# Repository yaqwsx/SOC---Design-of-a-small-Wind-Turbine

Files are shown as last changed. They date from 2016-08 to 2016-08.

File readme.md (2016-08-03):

Český popis k nalezení níže.

# Design of a Small Wind Turbine

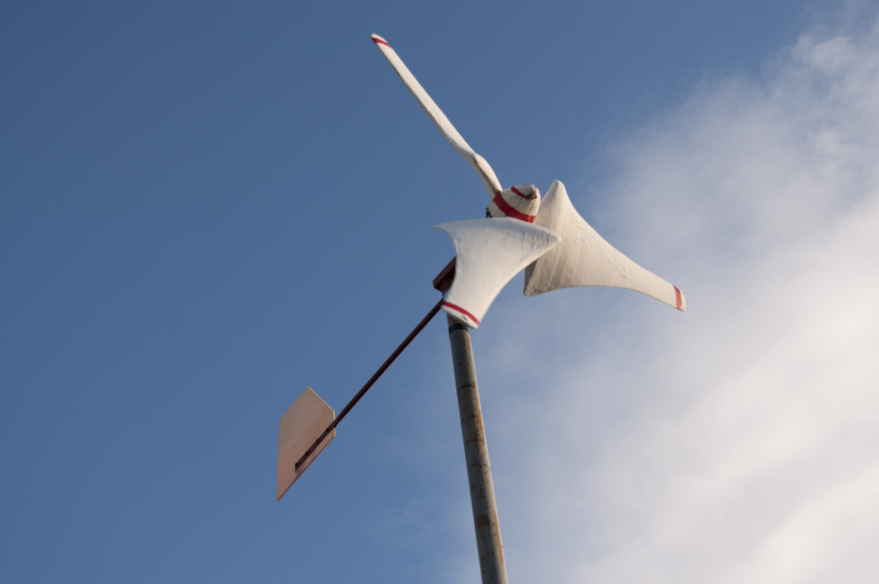
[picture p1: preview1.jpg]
preview1


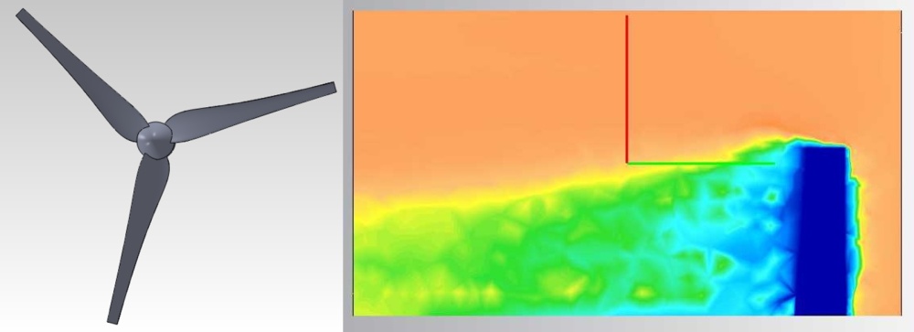
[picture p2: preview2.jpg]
preview2


This is a backup of my high school project created back in 2012. It is a direct
copy, without any modification. Because I was stupid when I was a kid, the
source is quite messy.

I explore aerodynamics principles of wind turbines in this thesis and based on
these principles I design a small turbine width diameter 2.5 meters. I discuss
aspects of its efficiency, startability and ways to reduce induced loss. The
induced losses were explored by a FEM simulation.

The whole thesis in Czech, but even though you might want to check out the [final
version](text_v2/final.pdf) - there are lots of images and a nice formulas! The
thesis won a 2nd place in [SOČ](http://soc.cz).

Small note: Three years later I build a turbine according design in this theses.
However there are no photos, as my SD card with them died. Since then, I backup!
(and you should too). See more at [Aurae repostiory](https://github.com/yaqwsx/Aurae).

# Návrh malé větrné turbíny

Tento repozitář je záložní kopií mého středoškolského projektu z roku 2012.
Projekt nebyl nijak modifikován a je v původní (lehce chaotické) verzi.

Práce se zabývá aerodynamikou malých větrných turbín a zejména jejich návrhem.
Popisuje návrh malé horizontální větrné turbíny o průměru 2,5 m. Zkoumá různé
aspekty její účinnosti, zabývá se její startovatelností a omezením indukovaných
ztrát. Práce dále popisuje také stavbu druhé menší turbíny založené na
zjednodušeném výpočtu.

Práce vyhrála 2. místo na [SOČ](http://soc.cz). Finální verze textu je k
nalezení [zde](text_v2/final.pdf).

Poznámka na závěr: Tři roky po napsání této práce jsem skutečně postavil turbínu
popisovou v této práci. Bohužel k ní nemám žádnou dokumentaci, jelikož SD karta
s veškerými fotografiemi umřela. Od té doby zálohuji! Více informací je k nalezení
v [repozitáři Aurae](https://github.com/yaqwsx/Aurae).

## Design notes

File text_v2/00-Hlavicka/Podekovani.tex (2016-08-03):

\vfill

\vglue 14cm

\section*{Poděkování}

\begin{spacing}{1.3}
Chtěl bych poděkovat zejména mému otci, který mě v~celém mém bádání podporuje a poskytuje mi pomoc v~konstrukčních stránkách celé stavby. 
\end{spacing}

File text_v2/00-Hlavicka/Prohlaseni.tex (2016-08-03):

\vfill

\vglue 13cm

\section*{Prohlášení}

\begin{spacing}{1.3}
	 Prohlašuji, že jsem svou práci vypracoval samostatně, použil jsem pouze podklady (literaturu, software, atd.) uvedené v této práci a postup při zpracování a dalším nakládání s prací je v souladu se zákonem č. 121/2000 Sb., o právu autorském, o právech souvisejících s právem autorským a o změně některých zákonů (autorský zákon) v~platném znění. 
\end{spacing}

\vspace{1.5cm}

V~Hulíně dne \Podepsano

\begin{flushright}
	\vspace{-1.5cm}
	\begin{tabular}{p{3.5cm}}
		\hspace{0.8cm}
		\\
		\hline
		\hspace{1cm} podpis
	\end{tabular}
	\hspace*{0.5cm}
\end{flushright}

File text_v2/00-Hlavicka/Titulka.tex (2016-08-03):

\pagestyle{empty}

\begin{center}
	{\LARGE \textsc \Skola}\\

	\vspace{4cm}

	{
		\textbf {\Huge \Jmeno \\[1ex]}
		\textbf {\Large \Kategorie \\[8ex]}
		{\Huge \bf \NazevCJ \\[2ex]}
		{\LARGE \bf \NazevAJ}
	}

	\vfill

	{\large  \Datum \hfill Autor: \Autor}\\[6ex]

	\newpage
\end{center}

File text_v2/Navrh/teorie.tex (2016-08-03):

\chapter{Teorie výpočtu}
\label{kap:teorie}
	V této kapitole bych rád čtenáře seznámil s teoretickými poznatky, ze kterých jsem při mém návrhu vycházel. Celá tato kapitola \ref{kap:teorie} je parafrázováním knihy \cite{Rychetnik:Motory} doplněné o některé mé postřehy a poznámky. Kapitola je rozdělena na dvě části – v první se zabývám teoretickou účinností větrných motorů. V druhé části popisuji funkci horizontální vztlakové turbíny a uvádím dva způsoby výpočtu.
	
	\section{Teoretická účinnost větrných turbín}\label{ucinnost}
	Jak jsem již zmínil v kapitole \ref{sec:typy_turbin}, základy funkce vztlakových turbín popsal Albert Betz. Ten odvodil maximální teoretickou účinnost větrných motorů. Na jeho počest je nazývána Betzova.
	
	Je několik různých způsobů výpočtů maximální účinnosti. Některé dávají vyšší a některé nižší hodnoty (např. maximální účinnost podle Sabinina je 68,7~\% \cite{Rychetnik:Motory}). Běžně se však v literatuře uvažuje právě Betzova účinnost. Tato účinnost je pouze teoretická. Skutečná účinnost je vždy značně nižší (aby se turbína mohla přiblížit ideální, nesměla by proudu vzduchu za ní udělovat rotační složku).
	V této kapitole bych rád ukázal, jak lze Betzovu účinnost odvodit. Odvození vychází z~obrázku~\ref{obr.rotor}:
	\begin{figure}[H]
		%\begin{center}
		\centering
			
	          %\input{obrazky/rotor2.ipe}
		\caption{Princip větrné turbíny. Proud vzduchu (v ploše $S_1$ s rychlostí $v_1$) vstupuje do roviny turbíny $S$. Zde je zpomalen a za rotorem vystupuje v ploše $S_2$ s rychlostí $v_2$. Inspirováno \cite{Rychetnik:Motory}.}
		\label{obr.rotor}
	    %\end{center}
	  \end{figure}
	
	Tento nákres znázorňuje proud vzduchu procházející rotorem. Za předpokladu, že se tento proud nemísí s okolním vzduchem, je soustava izolovaná a platí zde rovnice kontinuity \eqref{rov:1}\cite{Rychetnik:Motory}:
	
	\begin{equation}
		S_1 v_1 = Sv = S_2 v_2\label{rov:1}
	\end{equation}
	Poté lze za zákona zachování hybnosti odvodit axiální sílu $F_a$ působící na rotor \eqref{rov:2}\cite{Rychetnik:Motory}:
	\begin{eqnarray}
		\label{rov:2}
		\Delta p = p_1 - p_2 \nonumber \\
		F\Delta t=mv_1 - mv_2 \nonumber \\
		F\Delta t = \rho Sv\Delta t(v_1 - v_2) \nonumber \\
		F_a = \rho Sv(v_1 - v_2)
	\end{eqnarray}
	Z axiální síly $F_a$ lze spočítat i výkon turbíny \eqref{rov:3}\cite{Rychetnik:Motory}:
	\begin{equation}
		\label{rov:3}
		P = F_a v = \rho Sv^2 (v_1 - v_2)
	\end{equation}
	Výkon turbíny lze také spočítat i pomocí změny kinetické energie proudu vzduchu \eqref{rov:4}\cite{Rychetnik:Motory}:
	\begin{equation}
			\label{rov:4}
			P = \frac{\Delta E_k}{\Delta t} = \frac{1}{2} \rho Sv(v_1^2 - v_2^2)
	\end{equation}
	Porovnáním různě vyjádřeného výkonu z rovnice \ref{rov:3} a \ref{rov:4} vyplývá, že rychlost v rovině rotoru je aritmetickým průměrem rychlosti před a za rotorem \eqref{rov:5}\cite{Rychetnik:Motory}:
	\begin{equation}
			\label{rov:5}
			P_p = P_{E_k} \Rightarrow v=\frac{v_1 + v_2}{2}
	\end{equation}
	Díky tomuto poznatku lze vyjádřit axiální sílu $F_a$ i výkon $P$ pouze v závislosti na rychlosti proudu větru před a za rotorem\eqref{rov:6}\cite{Rychetnik:Motory}:
	\begin{eqnarray}
		\label{rov:6}
		F_a = \frac{1}{2}\rho S(v_1^2 - v_2^2) \nonumber \\
		P=\frac{1}{4}\rho S(v_1^2 - v_2^2)(v_1 + v_2)
	\end{eqnarray}
	Účinnost můžeme vyjádřit jako poměr výkonu turbíny a výkonu proudu vzduchu vstupujícího do turbíny vzduchu\eqref{rov:7}\cite{Rychetnik:Motory}. Výkon proudu vzduchu lze určit pomocí kinetické energie tohoto proudu.
	\begin{equation}
		\label{rov:7}
		\eta = \frac{\frac{1}{4}\rho S(v_1^2 - v_2^2)(v_1 + v_2)}{\frac{1}{2}\rho Sv_1^3}=\frac{(v_1^2 - v_2^2)(v_1 + v_2)}{2v_1^3}
	\end{equation}
	Pokud vyjádříme poměr rychlostí proudu vzduchu před a za rotorem následovně\eqref{rov:8}\cite{Rychetnik:Motory}:
	\begin{equation}
		\label{rov:8}
		k= \frac{v_2}{v_1}
	\end{equation}
	Lze rovnici \eqref{rov:7} zjednodušit na tvar \eqref{rov:9}
	\begin{equation}
		\label{rov:9}
		\eta = \frac{(k+1)(1-k^2)}{2}
	\end{equation}
	Derivací tohoto výrazu můžeme zjistit jeho maximum\eqref{rov:10}:
	\begin{eqnarray}					\label{rov:10}
		\frac{\mathrm{d}}{\mathrm{d}k}(\frac{(k+1)(1-k^2)}{2})=\frac{-3k^2}{2}-k+\frac{1}{2} \nonumber \\
		\frac{-3k^2}{2}-k+\frac{1}{2}=0 \Rightarrow k=\{-1;\frac{1}{3}\}
	\end{eqnarray}
	Výraz \ref{rov:10} má maximální hodnotu na intervalu $<0;1>$ (jiné hodnoty poměru rychlostí nedávají smysl) pro $k=\frac{1}{3}$. Při tomto poměru rychlostí vychází $\eta =\frac{16}{27}\doteq 59~\%$, což je hledaná Betzova teoretická účinnost. Průběh účinnosti v závisloti na poměru rychlostí lze vidět na grafu \ref{graf.ucinnost}.
	\begin{figure}[H]
		%\begin{center}
		\centering
			
	          %\input{obrazky/rotor2.ipe}
		\caption{Průběh Betzovy účinnosti pro jednotlivé poměry $v_1/v_2$}
		\label{graf.ucinnost}
	    %\end{center}
	  \end{figure}
	  
	\section {Aerodynamika horizontální vztlakové turbíny}
	V této kapitole shrnuji veškeré důležité teoretické poznatky pro výpočet větrné turbíny. Tyto poznatky jsou poté použity k výpočtu parametrů turbíny v kapitole \ref{chap:praxe}.
	
	Tuto kapitolu jsem rozdělil na tři části. V první části (kapitola \ref{kap:zakladprinc}) jsou vysvětleny základní principy a pojmy ohledně aerodynamických profilů – základního stavebního prvku vztlakových turbín.
	
	Druhá část (kapitola \ref{kap:funkce1}) vysvětluje funkci turbíny a odvozuje základní výpočet. Na tuto kapitolu navazuje kapitola \ref{kap:funkce2}, která tento výpočet rozšiřuje o vírovou teorii.
	
	\subsection{Základní princip, aerodynamický profil}\label{kap:zakladprinc}
	Jak jsem zmínil v předchozích kapitolách, základním principem vztlakových turbín je síla vznikající na rotorovém listu při obtékání vzduchem. Tato síla vzniká díky tvarování listu – podobně jako na křídle letadla. List má v průřezu tvar aerodynamického profilu.
	
	Aerodynamický profil lze nejlépe charakterizovat pomocí obrázku \ref{obr.profil}:
	
	\begin{figure}[H]
		\centering
		
		\caption{Charakteristika aerodynamického profilu. Inspirováno \cite{Rychetnik:Motory}}
		\label{obr.profil}
	\end{figure}
	
	Profily mají různý tvar; zpravidla jsou však na své náběžné hraně zakulacené a směrem k~odtokové hraně se sbíhají do ostrého konce. Spojnice odtokové hrany s~náběžnou se nazývá tětiva profilu. Zpravidla se značí~$b$. Úhel, který svírá tětiva profilu se směrem pohybu proudu vzduchu (rychlost je zde označena jako $v$), se nazývá úhel náběhu. Běžně se označuje $\alpha$. Často se úhlem $\alpha$ automaticky myslí optimální úhel náběhu, při kterém profil vykazuje nejlepší vlastnosti (poměr sil $F_y$ a $F_x$ je největší). Na obrázku je také vyznačen úhel $\alpha _0$ – úhel nulového vztlaku. Při tomto úhlu náběhu nevzniká na profilu žádná vztlaková síla\cite{Rychetnik:Motory}.
	
	Při obtékání profilu proudem vzduchu vzniká síla $F$. Její velikost a směr jsou závislé na úhlu~$\alpha$. Síla zde vzniká díky vyšší rychlosti obtékajícího vzduchu na vztlakové (na nákresu se jedná o horní stranu) než na podtlakové (spodní) straně. Podle Bernoulliho rovnice klesá v~rychleji se pohybujícím proudu vzduchu statický tlak. Tento podtlak vyvolává vztlakovou sílu\cite{Rychetnik:Motory}.
	
	Pro další úvahy je vhodné rozdělit sílu $F$ na dvě navzájem kolmé složky – $F_x$ a $F_y$. Sílu $F_y$, která je kolmá na směr pohybu proudu vzduchu, nazýváme vztlaková (anglicky označována jako lift force). Sílu $F_x$ nazýváme odporovou (anglicky drag force). Tato síla působí proti směru pohybu profilu a je nežádoucí – snižuje účinnost rotoru\cite{Rychetnik:Motory}\cite{ve:ve}.
	
	Velikost těchto sil je možno spočítat pomocí součinitele vztlaku $c_y$ (v anglické literatuře označován jako $c_L$ – lift coefficient) a součinitele odporu $c_x$ (ang. $c_d$, drag coefficient). Tyto součinitelé jsou vždy platní pouze pro určitý úhel náběhu a Reynoldsovo číslo (viz dále). Dají se zjistit experimentálně, případně pomocí CFD simulace. Na základě těchto součinitelů lze síly $F_x$ a $F_y$ spočítat následovně \eqref{rov:11}\cite{Rychetnik:Motory}:
	
	\begin{eqnarray}
			\label{rov:11}
			F_x \frac{1}{2}\rho c_x Sv^2 \nonumber \\
			F_y \frac{1}{2}\rho c_y Sv^2
	\end{eqnarray}
	Kde $\rho$ označuje hustotu vzduchu, $v$ rychlost proudu vzduchu a $S$ plochu listu. V dalších kapitolách bude často uvažována nekonečně malá část rotorového listu a za $S$ se bude dosazovat $dS$, které lze definovat následovně\eqref{rov:12}\cite{Rychetnik:Motory}: 
	
		\begin{equation}
				\label{rov:12}
				S=b\;\mathrm{d}r
		\end{equation}
	Kde $\mathrm{d}r$ je nekonečně malá vzdálenost mezi 2 poloměry $r_1$ a $r_2$ na rotorovém listu a $b$ je délka tětivy.
	
	Na grafech \ref{graf:zavislost1} a \ref{graf:zavislost2} je znázorněn průběh součinitelů vztlaku a odporu v závislosti na úhlu náběhu pro profil SG6043 (při Reynoldsově čísle $10^5$).
	
	\begin{figure}[H]
	\centering
	\subfigure[Závislost součinitele vztlaku na úhlu náběhu. ]{\label{graf:zavislost1}}~
	\subfigure[Závislost součinitele odporu na úhlu náběhu. ]{\label{graf:zavislost2}}
	\caption{Závislosti součinitelů $c_x$ a $c_y$ u profilu SG6043 při $Re=10^5$. Data převzata z \cite{profil}}
	\end{figure}
	
	Jak jsem zmínil výše, aerodynamické vlastnosti profilu nejsou vždy stejné. Pro charakteristiku podmínek, při kterých byly naměřeny dané hodnoty, se používá Reynoldsovo číslo $Re$. Jedná se o bezrozměrnou veličinu popisující proudění. Reynoldsovo číslo je definováno následovně\eqref{rov:13}\cite{Rychetnik:Motory}:
	\begin{equation}
					\label{rov:13}
					Re=\frac{vl}{\nu}
	\end{equation}
	Kde ve vztahu \eqref{rov:13} $v$ je rychlost obtékání profilu, $l$ je délka tětivy a $\nu$ je kinematická viskozita vzduchu.
	
	Reynoldsovo číslo se pohybuje pro malé rotory (do 10~m) v rozmezí $10^5$–$10^7$\cite{ve:ve}. Ze vzorce je patrné, že Reynoldsvo číslo je pouze orientační údaj – ve vzorci vystupuje rychlost obtékání a~délka tětivy. Obě tyto veličiny se u listů větrné turbíny mění v závislosti na vzdálenosti od osy otáčení. Proto se také často počítá se zaokrouhlenou hodnotou kinematické viskozity vzduchu $1,5\cdot 10^{-6}\;m\cdot s^{-2}$\cite{Rychetnik:Motory}.
	
	\subsection{Funkce horizontální vztalkové turbíny}\label{kap:funkce1}
	Cílem této kapitoly je objasnit, jaký tvar (úhel náběhu a délku tětivy) by rotorový list měl mít, aby dosahoval co nejlepších vlastností.
	
	Na otáčející se turbíně se nachází rotorový list v~situaci na obrázku \ref{obr.profilprostor}).
	
	\begin{figure}[H]
		\centering
		
		\caption{Rotorový list na otáčející se turbíně. Inspirováno \cite{Rychetnik:Motory}.}
		\label{obr.profilprostor}
	\end{figure}
	Obrázek \ref{obr.profilprostor} zobrazuje část (řez) rotorového listu na poloměru $r$. Celý list se otáčí úhlovou rychlostí $\omega$, prvek na poloměru $r$ má pak tedy obvodovou rychlost $u$ \eqref{rov:14}\cite{Rychetnik:Motory}:
	\begin{equation}
		\label{rov:14}
		u=\omega r=\frac{\pi n}{30}r
	\end{equation}
	Kde $n$ jsou otáčky za minutu, které jsou zde uvedeny, jelikož jsou pro představu názornější než úhlová rychlost. Rovnoběžně s~osou otáčení fouká vítr rychlostí $v$. Je důležité si všimnout orientace profilu listu – tlaková strana je nastavena proti směru větru. Je tedy opačně orientován než u běžných leteckých vrtulí. U leteckých vrtulí má list opačnou funkci – místo zpomalování proud vzduchu jej urychluje.
	
	Vektorovým součtem obvodové rychlosti $u$ a rychlosti větru $v$ získáváme relativní rychlost větru $w$. Platí tedy \eqref{rov:15}\cite{Rychetnik:Motory}.
	\begin{equation}
		\label{rov:15}
		w=\sqrt{u^2 + v^2}
	\end{equation}
	Rychlostí $w$ (a v jejím směru) je rotorový list ofukován. Na obrázku je vyznačen úhel $\beta$, který rychlost $w$ svírá s~osou otáčení. Z~obrázku je tedy patrný vztah \eqref{rov:16}\cite{Rychetnik:Motory}:
	\begin{equation}
		\label{rov:16}
		\tan{\beta}=\frac{v}{u}
	\end{equation}
	Z rovnice \eqref{rov:16} vyplývá důležitý poznatek – jelikož je rychlost v konstantní a obvodová rychlost u závisí na poloměru $r$, nemá rotorový list po celé své délce stejný úhel náběhu. Obdobně se dá předpokládat, že ani délka tětivy $b$ nebude po celé délce listu konstantní. Proto musí být veškeré úvahy prováděny na (nekonečně) malém úseku mezi poloměrem $r$ a $r + \mathrm{d}r$.
	
	Úhel $\alpha$, který svírá tětiva profilu s~relativní rychlostí proudu vzduchu, zde značí optimální úhel náběhu – poměr součinitelů $c_y/c_x$ je největší možný pro daný profil.
	
	Na rotorovém listu při obtékání vzduchem vzniká vztlaková síla. Tu můžeme rozložit podle obrázku \ref{obr.profilsil}.
	\begin{figure}[h]
		\centering
		
		\caption{Rozklad sil na rotorovém listu. Inspirováno \cite{Rychetnik:Motory}.}
		\label{obr.profilsil}
	\end{figure}
	Síly $F_x$ a $F_y$ lze spočítat z rovnice \ref{rov:11}. Jejich výslednice lze rozložit na 2 složky – sílu $F_t$, která otáčí rotorem, a sílu $F_a$, která působí na stožár a na užitečném výkonu turbíny se nepodílí. Síla $F_t$, respektive její element $\mathrm{d}F_t$ na prvku $r$, vyvolává elementární moment síly dle \eqref{rov:17}\cite{Rychetnik:Motory}.
	\begin{equation}
		\label{rov:17}
		\mathrm{d}M=\mathrm{d}F_t r
	\end{equation}
	Jelikož se v dalších výrazech vyskytuje úhel $\beta$, je vhodné vyjádřit $w$ také pomocí úhlu $\beta$ \eqref{rov:18}\cite{Rychetnik:Motory}:
	\begin{eqnarray}
				\label{rov:18}
			u=v \cot\beta \nonumber \\
			w^2 = 1 + cotg^2 \beta
	\end{eqnarray}
	Poté lze vyjádřit sílu v axiálním směru ve tvaru \eqref{rov:19}\cite{Rychetnik:Motory}.
	\begin{equation}
		\label{rov:19}
		\mathrm{d}F_a=\frac{1}{2}v^2\rho\;\mathrm{d}S(1+cotg^2 \beta)(c_y \cos \beta + c_x \sin \beta)
	\end{equation}
	Kde $(c_y \cos\beta+c_x \sin \beta)$ vychází z obrázku \ref{obr.odvozeni1}.
	\begin{figure}[H]
		\centering
		\subfigure[Zde lze vidět, že síla $F_a$ je složena z~přilehlé odvěsny přepony velkého trojúhelníku s~úhlem $\beta$ a protihlehlé odvěsny malého trojúhelníku s~úhlem~$\beta$ ]{\label{obr.odvozeni1}}~
		\subfigure[Zde lze vidět, že síla $F_t$ je rovna protilehlé odvěsně velkého trujúhelníku s~úhlem $\beta$ mínus přilehlá odvěsna malého trojúhelníku s~úhlem~$\beta$]{\label{obr.odvozeni2}}
		\caption{Odvození vztahů pro síly na profilu}
	\end{figure}
	Obdobně lze vyjádřit i element síly $F_t$ \eqref{rov:20}\cite{Rychetnik:Motory}.
	\begin{equation}
			\label{rov:20}
			\mathrm{d}F_t=\frac{1}{2}v^2\rho\;\mathrm{d}S(1+cotg^2 \beta)(c_y \sin \beta - c_x \cos \beta)
	\end{equation}
	V knize \cite{Rychetnik:Motory} se ve výrazu \eqref{rov:20} nachází chyba (překlep), kdy je v poslední závorce znaménko plus místo mínus. Důkaz znaménka mínus vyplývá z obrázku \ref{obr.odvozeni2}.
	
	Z výše vyjádřené síly $F_t$ lze určit elementární moment a elementární užitečný výkon vznikající na daném prvku rotoru \eqref{rov:21}\cite{Rychetnik:Motory}.
	\begin{eqnarray}
		\label{rov:21}
		\mathrm{d}M=\frac{1}{2}v^2\rho \; \mathrm{d}Sr(1+cotg^2 \beta) (c_y\sin\beta - c_x\cos \beta)\nonumber \\
		\mathrm{d}P_u=\mathrm{d}M\omega=\mathrm{d}M\frac{u}{r}=\mathrm{d}M\frac{v \cot\beta}{r}\nonumber \\
		\mathrm{d}P_u=\frac{1}{2}v^3\rho\;\mathrm{d}S(1+cotg^2 \beta)(c_y\sin \beta-c_x\cos\beta)\cot\beta
	\end{eqnarray}
	Tímto byly shrnuty veškeré základní poznatky, které je nutno o vztlakové horizontální turbíně vědět. Zbývá už jen z~těchto poznatků vyjádřit, jak má co nejideálnější turbína vypadat.
	
	Základním parametrem větrné turbíny je již dříve zmíněná rychloběžnost. Zpravidla se značí~$\lambda$ (někdy se lze setkat i s~označením $\lambda_0$). Jedná se o bezrozměrnou veličinu, která popisuje poměr obvodové rychlosti turbíny $u_R$ vůči rychlosti větru před turbínou $v_1$\eqref{rov:22}\cite{Rychetnik:Motory}.
	\begin{equation}
			\label{rov:22}
			\lambda = \frac{u_R}{v_1}
	\end{equation}
	Tento parametr turbíny se zpravidla volí (odvisí od něj otáčky rotoru), je však omezen daným typem turbíny. Například rotor Savonius je schopný efektivně pracovat při rychloběžnosti 0,85–1,8, \uv{americké kolo} 1,1–2, třílistá horizontální turbína 2–6, dvoulistá 6–10. Třílistý rotor Darrieus 4,6–6,8 a jednolistý 6–10. Tyto údaje byly převzaty z~\cite{Rychetnik:Motory} a~\cite{ve:ve}. Z~předchozích poznatků vyplývá, že ideální rotor má konstantní rychloběžnost a tudíž je neregulovatelný. Jakoukoliv regulaci otáček je možné provést pouze za cenu snížení účinnosti.
	
	Můžeme také definovat rychloběžnost pro prvek na listu ve vzdálenosti $r$ od středu \eqref{rov:23}\cite{Rychetnik:Motory}.
	\begin{equation}
		\label{rov:23}
		\lambda_r = \frac{u_r}{v_1}=\frac{r}{R}\lambda
	\end{equation}
	V kapitole \ref{ucinnost} vyplynulo z Betzovi účinnosti, že rotor má maximální účinnost právě tehdy, platí-li \eqref{rov:24}.	
	\begin{equation}
			\label{rov:24}
			v_2 = \frac{1}{3}v_1
	\end{equation}
	Z rovnice \eqref{rov:5} v kapitole \ref{ucinnost} vyplývá, že rychlost v rovině rotoru $v$ je rovna \eqref{rov:25}\cite{Rychetnik:Motory}.
	\begin{equation}
		\label{rov:25}
		v = \frac{v_1+v_2}{2}=\frac{v_1+\frac{1}{3}v_1}{2}=\frac{2}{3}v_1
	\end{equation}
	Díky vyjádření z~rovnice \eqref{rov:25} lze dosazením do rovnice \eqref{rov:16} spočítat~$\beta$ pro jednotlivé prvky listu ve vzdálenosti~$r$ od středu rotoru\eqref{rov:26} – tedy jednu ze dvou charakteristik tvaru listu (druhou je délka tětivy)\cite{Rychetnik:Motory}.
	\begin{eqnarray}
		\label{rov:26}
		\tan\beta=\frac{v}{u_r}=\frac{\frac{2}{3}v_1}{\lambda_r v_1}=\frac{2}{\frac{3r\lambda}{R}} \nonumber \\
		\beta = \arctan(\frac{2R}{3r\lambda})
	\end{eqnarray}
	K tomuto vyjádření je nutné připomenout obrázek \ref{obr.profilprostor}. Z~něj je patrné, že úhel $\beta$ není odchylkou tětivy profilu od roviny rotoru. Odchylku tětivy profily je úhel $\varphi$, který lze určit dle \eqref{rov:27}.
	\begin{equation}
		\label{rov:27}
		\varphi = \beta - \alpha
	\end{equation}
	Kde $\alpha$ je optimální úhel náběhu daného aerodynamického profilu.
	
	Délku tětivy lze spočítat z předpokladu, který vyplývá z Betzovy účinnosti – proud vzduchu musí být turbínou zpomalen na $\frac{1}{3}$  své původní rychlosti. Proud vzduchu vyvolává na rotoru axiální sílu. Axiální sílu působící na jeden element rotoru lze změnou hybnosti vyjádřit dle \eqref{rov:28}\cite{Rychetnik:Motory}.
	\begin{eqnarray}
		\label{rov:28}
		\mathrm{d}F_a=\rho\; \mathrm{d}V(v_1 - v_2) \nonumber \\
		\mathrm{d}V=2\pi r \; \mathrm{d}r\frac{v_1+v_2}{2} \nonumber \\
		\mathrm{d}F_a=2\pi\rho r\; \mathrm{d}r\frac{v_1+v_2}{2}(v_1-v_2)
	\end{eqnarray}
	Axiální sílu lze však vyjádřit i pomocí aerodynamických sil (jak je popsáno v rovnici \eqref{rov:19}). Kniha \cite{Rychetnik:Motory} tento výpočet dle mě zbytečně zjednodušuje – zanedbává vliv odporové síly vznikající na profilu listu. Já jej však budu nadále uvažovat. Rovnice \eqref{rov:19} však představuje sílu působící pouze na jeden list; celková síla axiální síla je \eqref{rov:29}:
	\begin{equation}
			\label{rov:29}
			\mathrm{d}F_a=\frac{1}{2}v^2z\rho\;\mathrm{d}S(1+cotg^2 \beta)(c_y \cos \beta + c_x \sin \beta)
	\end{equation}
	Kde $z$ je počet listů rotoru.
	
	Porovnáním dvou vyjádření axiální síly a dosazením vztahů \eqref{rov:28} a \eqref{rov:29} lze získat vztah \eqref{rov:30} vyjadřující délku tětivy $b$ pro element listu na poloměru $r$.
	
	\begin{eqnarray}
		\label{rov:30}
		2\pi\rho r\; \mathrm{d}r\frac{v_1+v_2}{2}(v_1-v_2)=\frac{1}{2}\left( \frac{v_1 + v_2}{2} \right)^{2} z\rho b\;\mathrm{d}r(1+cotg^2 \beta)(c_y \cos \beta + c_x \sin \beta) \nonumber \\
		2\pi r(v_1-v_2)=\frac{1}{2} zb(1+cotg^2 \beta)(c_y \cos \beta + c_x \sin \beta)\left( \frac{v_1 + v_2}{2} \right) \nonumber \\
		2\pi r\frac{2}{3}v_1=\frac{1}{2} zb(1+cotg^2 \beta)(c_y \cos \beta + c_x \sin \beta )\frac{2}{3}v_1 \nonumber \\
		b=\frac{4\pi r}{z(1+cotg^2 \beta)(c_y \cos \beta + c_x \sin \beta )}
	\end{eqnarray}
	Toto vyjádření není v ideální podobě (bylo by vhodné ještě vyjádřit funkce úhlu $\beta$ pomocí poloměru a rychloběžnosti), ale i přesto poskytuje jasnou představu o délce tětivy na listu.
	
	Na grafech \ref{graf.delka1} a \ref{graf.nabeh1} lze najít průběh délky tětivy a úhlu odchylky tětivy od rotoru na prvním prototypu větrné turbíny. Je zde zahrnuto i porovnání výpočtu uvažujícího odporovou sílu a výpočtu, který ji neuvažuje.
	
	\begin{figure}[H]
			%\begin{center}
			\centering
				
		          %\input{obrazky/rotor2.ipe}
			\caption{Délka tětivy prvního prototypu trubíny. Turbína má tři listy, rychloběžnost 4, a poloměr 75~cm. Používá profil SG6043 s $c_x$ 1,303 a $c_y$ 0,017. Je zde patrný minimální rozdíl mezi výpočtem s~odporem a bez odporu.}
			\label{graf.delka1}
		    %\end{center}
		  \end{figure}
		  
	\begin{figure}[H]
				%\begin{center}
				\centering
					
			          %\input{obrazky/rotor2.ipe}
				\caption{Graf znázorňující průběh odchylky tětivy od roviny rotoru a úhel relativní rychlosti vzduchu. Je zde uvažován ideální úhel náběhu profilu SG6043 $5,5\,^{\circ}$.}
				\label{graf.nabeh1}
			    %\end{center}
	\end{figure}

	\subsection{Rozšířený výpočet, vírová teorie}\label{kap:funkce2}
	
	Výpočet tvaru listu v předchozí kapitole má jeden nedostatek – předpokládá, že turbína proudu za rovinou rotoru neuděluje žádnou rotační složku. Avšak této vlastnosti může dosáhnout pouze ideální turbína, jejíž lopatky jsou nekonečně tenké a nevznikají na nich žádné třecí síly.
	
	Teorii uvažující vír vznikající za rotorem poprvé popsal britský aerodynamik Hermann Glauert. V této kapitole tuto teorii popisuji. Na konci této kapitoly uvádím porovnání výsledků výpočtů zjednodušené a Glauertovy teorie.
	
	Glauertova vírová teorie předpokládá, že proud vzduchu před rotorem má nulovou rotační složku (úhlová rychlost je nulová). Po průchodu rotorem bude proudu vzduchu udělena úhlová rychlost $\Omega$. Stejně jako v předchozí teorii, platí, že rychlost $v$~v rovině rotoru je aritmetickým průměrem rychlosti před rotorem $v_1$ a rychlosti za rotorem     $v_2$. Obdobně je i úhlová rychlost proudu v rovině aritmetickým průměrem rychlosti před rotorem a za ním; tedy $\frac{\Omega}{2}$\cite{Rychetnik:Motory}.
	
	Pro další úvahy je vhodné vyjádřit přírůstek úhlové rychlosti proudu vzduchu k~úhlové rychlosti rotoru $\omega$ pomocí koeficientu $h$ a poměr rychlostí před a za rotorem pomocí koeficientu~$k$.
	
	Jelikož má tento vír opačný směr otáčení než rotor, platí výraz \eqref{rov:31}\cite{Rychetnik:Motory}.
	
		\begin{eqnarray}
			\label{rov:31}
			\omega + \Omega = h\omega \nonumber \\
			\Omega = (h-1)\omega
		\end{eqnarray}
	Obdobně lze vyjádřit poměr rychlostí $v_1$ a $v_2$ \eqref{rov:32}\cite{Rychetnik:Motory}.
	\begin{eqnarray}
				\label{rov:32}
				k = \frac{v_2}{v_1} \nonumber \\
				v_2 = kv_1
	\end{eqnarray}
	Úhlovou rychlost proudu v rovině rotoru lze pomocí koeficientu vyjádřit následovně \eqref{rov:33}\cite{Rychetnik:Motory}:
	\begin{equation}
		\label{rov:33}
		\omega + \frac{\Omega}{2}=\frac{1+h}{2}\omega
	\end{equation}
	Stejně tak rychlost proudu vzduchu v rovině rotoru $v$ lze vyjádřit pomocí koeficientu $k$ - vztah \eqref{rov:34}\cite{Rychetnik:Motory}:
	\begin{equation}
			\label{rov:34}
			v =\frac{v_1 + v_2}{2}=\frac{1+k}{2}v_1
	\end{equation}
	Dalším cílem je pomocí nově definovaných rychlostí určit úhel relativní rychlosti proudu vzduchu $\beta$. Jeho určení je podobné jako ve zjednodušené teorii – vychází z obrázku \ref{obr.profilprostor}.
	Pro vyjádření úhlu $\beta$ je zapotřebí znát obvodovou rychlost prvku na rotoru ve vzdálenosti $r$ od osy otáčení \eqref{rov:35}\cite{Rychetnik:Motory}.
	\begin{equation}
		\label{rov:35}
		u =\frac{1+h}{2}\omega r
		\end{equation}
	Úhel $\beta$, který svírá směr relativní rychlosti proudu vzduchu $w$ s rovinou rotoru, lze potom vyjádřit následovně \eqref{rov:36}\cite{Rychetnik:Motory}:
	\begin{equation}
			\label{rov:36}
			\cot \beta = \frac{u}{v}=\frac{\frac{1+h}{2}\omega r}{\frac{1+k}{2}v_1}=\frac{1+h}{1+k}\lambda_r
	\end{equation}
	Velikost rychlosti $w$ je z~obrázku \ref{obr.profilprostor} rovna\eqref{rov:37}\cite{Rychetnik:Motory}:
	\begin{equation}
		\label{rov:37}
		w=\frac{v_1 (1+k)}{2\sin\beta}=\frac{\omega r(1+h)}{2\cos\beta}
	\end{equation}
	Další kroky jsou v podstatě stejné jako u zjednodušené teorie – je tedy nutné vyjádřit jednotlivé síly působící na elementy rotorového listu pomocí základní aerodynamiky vzduchového proudu a aerodynamických vlastností profilu listu. Pouze se zde dosazují výše odvozené rychlosti.
	
	Tudíž z výše uvedených vztahů lze sestavit rovnici pro axiální sílu $F_a$ - vztah \eqref{rov:38}\cite{Rychetnik:Motory}:
	\begin{equation}
		\label{rov:38}
	\mathrm{d}F_a = \mathrm{d}F_y\cos\beta+\mathrm{d}F_x\sin\beta = \frac{1}{2}\rho bw^2\; \mathrm{d}r(c_y\cos\beta + c_x\sin\beta)
	\end{equation}
	Obdobně lze také sestavit výraz pro tangenciální sílu $F_t$ \eqref{rov:39}. V~knize \cite{Rychetnik:Motory} je opět zaměněno znaménko.
	\begin{equation}
			\label{rov:39}
		\mathrm{d}F_t = \mathrm{d}F_y\sin\beta-\mathrm{d}F_x\cos\beta = \frac{1}{2}\rho bw^2\; \mathrm{d}r(c_y\sin\beta - c_x\cos\beta)
		\end{equation}
	Jelikož se zde objevují výrazy s~goniometrickými funkcemi, je výhodné převést vyjádření součinitelů vztlaku a odporu na goniometrický tvar. Celý převod vychází z obrázku \ref{obr.epsilon}.
	\begin{figure}[H]
					\centering
						
					\caption{Obrázek znázorňuje vyjádření sil $F_a$ a $F_t$ pomocí úhlu $\varepsilon$}
					\label{obr.epsilon}
				    %\end{center}
	\end{figure}
	Z obrázku \ref{obr.epsilon} vyplývá výraz \eqref{rov:40}\cite{Rychetnik:Motory}.
	\begin{equation}
		\label{rov:40}
		\tan \varepsilon = \frac{F_x}{F_y} = \frac{c_x}{c_y}
	\end{equation}
	Poté lze vyjádřit sílu $F_a$ následovně \eqref{rov:41}\cite{Rychetnik:Motory}:
	\begin{eqnarray}
		\label{rov:41}
		\cos \varepsilon = \frac{F_y}{F}\Rightarrow F=\frac{F_y}{\cos \varepsilon} \nonumber \\
		F_a = F\cos(\beta-\varepsilon)=\frac{F_y}{\cos\varepsilon}\cos(\beta-\varepsilon) \nonumber \\
		\mathrm{d}F_a=\frac{1}{2}\rho bw^2\;\mathrm{d}r\frac{c_y}{\cos\varepsilon}\cos(\beta - \varepsilon)
	\end{eqnarray}
	Obdobně lze vyjádřit i sílu Ft\eqref{rov:42}\cite{Rychetnik:Motory} a celkovou axiální sílu působící na všechny listy rotoru\eqref{rov:43}\cite{Rychetnik:Motory}.
	\begin{equation}
		\label{rov:42}
		\mathrm{d}F_t=\frac{1}{2}\rho bw^2\;\mathrm{d}r\frac{c_x}{\cos\varepsilon}\sin(\beta - \varepsilon)
	\end{equation}
	\begin{equation}
		\label{rov:43}
		\mathrm{d}F_{az}=\frac{1}{2}z\rho bw^2\;\mathrm{d}r\frac{c_y}{\cos\varepsilon}\cos(\beta - \varepsilon)
	\end{equation}
	Pomocí síly $F_t$ lze vyjádřit i celkový moment síly působící na všechny listy rotoru\eqref{rov:44}\cite{Rychetnik:Motory}.
	\begin{equation}
			\label{rov:44}
			\mathrm{d}M=rz\;\mathrm{d}F_t=\frac{1}{2}rz\rho bw^2\;\mathrm{d}r\frac{c_x}{\cos\varepsilon}\sin(\beta - \varepsilon)
		\end{equation}
	Axiální sílu na rotor lze stejně jako v odvození Betzovy účinnosti pomocí změny hybnosti proudu vzduchu. Proud vzduchu v~prstenci mezi poloměry $r$ a $r + \mathrm{d}r$ působí silou $\mathrm{d}F_a$ vyjádřené dle \eqref{rov:45}\cite{Rychetnik:Motory}.
	\begin{eqnarray}
		\label{rov:45}
		\mathrm{d}F_a\Delta t=m(v_1-v_2) \nonumber \\
		m=2\pi\rho r\;\mathrm{d}rv=\pi\rho r\;\mathrm{d}r(1+k)v_1 \nonumber \\
		\mathrm{d}F_a=\pi\rho r\;\mathrm{d}r(1+k)v_1\Delta v = \pi\rho r\;\mathrm{d}r(1-k^2)v_1^2
	\end{eqnarray}
	Moment síly na element rotoru mezi poloměry $r$ a $r + \mathrm{d}r$ lze také určit i ze změny momentu hybnosti proudu\eqref{rov:46}\cite{Rychetnik:Motory}. Jelikož je úhlová rychlost proudu před rotorem nulová, je změna úhlové rychlosti rovna $\Omega$.
	\begin{eqnarray}
		\label{rov:46}
		\mathrm{d}M = mru = mr^2\Omega \nonumber \\
		\mathrm{d}M=\rho\pi r^3\; \mathrm{d}r v_1(1+k)\Omega = \rho\pi r^3\; \mathrm{d}r v_1\omega(1+k)(h-1)
		\end{eqnarray}
		Další krok je podobný jako ve zjednodušené teorii – je nutné stejné, ale jinak vyjádřené, veličiny porovnat. Porovnáním axiální síly z rovnic \eqref{rov:43} a \eqref{rov:45} a dosazením relativní rychlosti proudu vzduchu $w$ z~rovnice \eqref{rov:37} dostaneme \eqref{rov:47}\cite{Rychetnik:Motory}.
		\begin{eqnarray}
			\label{rov:47}
			\frac{1}{2}\rho bzw^2\;\mathrm{d}r\frac{c_y}{\cos\varepsilon}\cos(\beta-\varepsilon)=\pi\rho r\;\mathrm{d}r(1-k^2)v_1^2 \nonumber \\
			\frac{1}{2} v_1^2\rho b \left(\frac{v_1(1+k)}{2\sin\beta}\right)^2\;\mathrm{d}r\frac{c_y}{\cos\varepsilon}\cos(\beta-\varepsilon)=\pi\rho r\; \mathrm{d}r(1-k^2)v_1^2 \nonumber \\
			c_y zb = \frac{8\pi r(1-k)\cos\varepsilon\sin^2 \beta}{\cos(\beta-\epsilon)(1+k)} \nonumber \\
			\frac{1-k}{1+k}=\frac{c_y zb \cos(\beta-\varepsilon)}{8\pi r \cos\varepsilon\sin^2\beta}
		\end{eqnarray}
		Stejnou úpravu je možné provést i s momentem síly vznikajícím na rotoru. Porovnáním rovnic \eqref{rov:44} a \eqref{rov:46} a dosazením rovnice \eqref{rov:37} dostaneme výraz \eqref{rov:48}\cite{Rychetnik:Motory}.
		\begin{eqnarray}
			\label{rov:48}
			\rho\pi r^3\;\mathrm{d}r v_1\omega(1+k)(h-1)=\frac{1}{2}rz\rho bw^2\;\mathrm{d}r\frac{c_x}{\cos \varepsilon}\sin(\beta-\varepsilon) \nonumber \\
			c_y zb = \frac{8\pi r(h-1)\cos\varepsilon\sin \beta \cos\beta}{\sin(\beta-\epsilon)(h+1)} \nonumber \\
			\frac{h-1}{h+1}=\frac{c_y zb \sin(\beta-\varepsilon)}{8\pi r \cos\varepsilon\sin\beta\cos\beta}
		\end{eqnarray}
		V knize \cite{Rychetnik:Motory} autor dává do poměru psolední řádky rovnic \eqref{rov:47} a \eqref{rov:48}. Tento postup je dle mě zbytečně složitý. Ekvivalentní výsledek, s jednodušší úpravou, lze získat porovnáním  vyjádření $c_yzb$ \eqref{rov:49}.
		\begin{eqnarray}
			\label{rov:49}
			\frac{8\pi r(1-k)\cos\varepsilon\sin^2 \beta}{\cos(\beta-\epsilon)(1+k)}=\frac{8\pi r(h-1)\cos\varepsilon\sin \beta \cos\beta}{\sin(\beta-\epsilon)(h+1)} \nonumber \\
			(1-k)(h+1)\sin(\beta-\varepsilon)\sin\beta=(h-1)(k+1)\cos\beta\cos(\beta-\varepsilon) \nonumber \\
			\frac{(1-k)(h+1)}{(h-1)(k+1)}=\frac{\cos\beta\cos(\beta-\epsilon)}{\sin\beta\sin(\beta-\epsilon)}=\cot(\beta-\varepsilon)\cot\beta
		\end{eqnarray}
		Zde je patrné, proč byla úprava poměru součinitelů $c_x$ a $c_y$ na $\tan\varepsilon$ (výraz \eqref{rov:40}) provedena – výrazně zjednodušila výsledný tvar.
		
		Ačkoliv to není přímo patrné, vyplývá z rovnice \eqref{rov:49} výpočet rotorového listu. Výpočet je složitější než v prvním případě. Jsou zde 2 proměnné (koeficienty $h$ a $k$), které jsou na sobě cyklicky závislé – jeden vyplývá z druhého. Tato soustava jde řešit pouze iteračně. Přesný postup výpočtu popisuji dále v kapitole \ref{postup}. Na grafu \ref{graf.glauert1} je zobrazeno porovnání délek tětiv zjednodušeného a Gluertova výpočtu. Tento graf je sestrojen pro turbínu stejných parametrů, na jaké byl konstruován první prototyp.
		
		Křivka grafu \ref{graf.glauert1}, která znázorňuje tvar listu, je velmi podobná vyobrazení ideálního rotoru na obrázku 5.2-5 v knize \cite{Crome:Technika} (strana 44). Je také vidět, že výpočet podle Glauerta dává výrazně jiné hodnoty v oblasti blízko osy otáčení než základní teorie.
		Porovnání úhlů náběhu mezi základním výpočtem a výpočtem podle Glauerta je zobrazeno na grafu \ref{graf.glauert2}. Hodnoty se výrazněji liší pouze blízko u osy otáčení (stejně jako v případě tětivy).

		\begin{figure}[h]
						%\begin{center}
						\centering
							
					          %\input{obrazky/rotor2.ipe}
						\caption{Graf porovánává délky tětiv pro zjednodušenou teorii a pro teorii podle Glauerta. List je počítán pro stejné parametry jako v grafu \ref{graf.delka1}}
						\label{graf.glauert1}
					    %\end{center}
		\end{figure}
		\begin{figure}[h]
								%\begin{center}
								\centering
									
							          %\input{obrazky/rotor2.ipe}
								\caption{Porovnání úhlu náběhu pro zjednodušenou teorii a výpočet podle Glauerta. List je počítán pro stejné parametry jako v grafu \ref{graf.delka1}}
								\label{graf.glauert2}
							    %\end{center}
				\end{figure}

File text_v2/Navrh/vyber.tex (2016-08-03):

\chapter{Výběr typu turbíny}
	Prvním krokem pro návrh větrné turbíny je určení typu. Každý typ má své specifické charakteristiky s~výhodami a nevýhodami. V~této kapitole jsem stručně popsal jednotlivé typy větrných turbín a rozebral jejich výhody a nevýhody. Na závěr kapitoly jsem ze zjištěných poznatků vybral vhodný typ větrné turbíny.	
	\section{Typy větrných turbín}\label{sec:typy_turbin}
		Větrné turbíny se běžně rozdělují na 2 základní skupiny podle principu – na odporové a vztlakové \cite{Rychetnik:Motory}.
		
		Odporové turbíny jsou z~historického hlediska starší. Základním principem těchto turbín je plocha, která klade větru odpor. Na této ploše vzniká síla, která rotorem otáčí. Plocha se však musí dostávat zpět na výchozí polohu. Běžně se používají 2 řešení\cite{Rychetnik:Motory}:
		
		\paragraph{Odporová plocha má různý odpor}
			Odporová plocha má při různých směrech obtékání různý aerodynamický odpor. Typickým příkladem je klasický miskový anemometr, jehož lopatky mají tvar duté polokoule. Polokoule má z vypouklé strany mnohem menší odpor než ze strany s~dutinou. Díky tomu se může miskový anemometr otáčet dokola. Na podobném principu pracuje i Savoniův rotor, který používá různě tvarované válcové plochy.
		\paragraph{Odporová plocha je natáčena}
			Plocha je v závislosti na pozici rotoru a směru větru natáčena. Toto řešení může dosahovat větší účinnosti než předchozí řešení s různým aerodynamickým odporem, ale je mnohem komplikovanější na výrobu a návrh.
			
		\bigskip	
		Díky jednoduchému principu lze sestrojit širokou škálu větrných turbín rozličných tvarů pracujících na odporovém principu. Lze sestrojit jak rotory s horizontální osou (anglicky označované jako HAWT – horizontal axis wind turbine), tak i s osou vertikální (anglicky označované jako VAWT – vertical axis wind turbine)\cite{ve:ve}.
		
		Dnes jsou nejpoužívanější turbíny pracující na vztlakovém principu. Základním principem je vztlak vznikající na listech turbíny. Tyto turbíny se používaly několik stovek let u větrných mlýnů; teoretické poznatky o jejich funkci jsou však mnohem mladší. Teoretické základy pro stavbu těchto turbín položil až na začátku 20. století německý fyzik Albert Betz\cite{betz}. Své první poznatky shrnul v knize  \uv{Das Maximum der theoretisch möglichen Ausnutzung des Windes durch Windmotoren}\cite{betz}.
		
		Turbíny lze sestrojit jak v horizontálním provedení, tak i vertikálním. Vertikální provedení si nechal patentovat francouzský inženýr aerodynamiky Georges Jean Marie Darrieus\cite{dar}. Běžně se tento typ turbíny označuje jako Darrieova turbína, či jen Darrieus.
		
		Horizontální provedení se dnes nejčastěji využívá u velkých větrných elektráren díky relativně snadné možnosti regulace otáček (oproti rotoru Darrieus). Horizontální turbíny se také dříve používaly jako pumpy na vodu – známé mnohalopatkové \uv{americké větrné kolo}\cite{ve:ve}.
	\section{Výběr typu turbíny}
		V předchozí kapitole jsem záměrně vynechal porovnání jednotlivých turbín. V této kapitole bych chtěl jednotlivé typy navzájem porovnat a vybrat nejvhodnější pro můj návrh.
		
		Odporové turbíny vynikají jednoduchou konstrukcí. Základní typy (např. Savoniův rotor) nejsou příliš náročné na přesnost výroby. Jejich nevýhodou je však nižší účinnost – Savoniův rotor dosahuje maximální účinnosti 23~\%, běžně však méně \cite{Rychetnik:Motory}. Fungují pouze při nízké rychloběžnosti (poměr obvodové rychlosti vůči rychlosti větru; viz. dále kapitola \ref{kap:funkce1}). Díky tomu dosahují malých otáček, což je nevhodné pro potenciální výrobu elektrické energie.
		
		Vztlakové turbíny mají vyšší účinnost (až 48~\%, většinou okolo 35~\%) \cite{Rychetnik:Motory} a větší rozsah použitelné rychloběžnosti. Jsou proto vhodné jak např. pro pumpování vody (pomaloběžné rotory), tak i jako rychloběžné pro výrobu elektrické energie. Jejich nevýhodou je však relativně větší náročnost na přesnost výroby a potřebné teoretické znalosti.
		
		Vertikální umístění rotoru má oproti horizontálnímu umístění výhodu v~odstranění nutnosti natáčet rotor vůči větru, navíc jsou méně náchylné na turbulence a víry v okolí. Díky tomu jsou schopny pracovat i relativně nízko u země a nepotřebují tedy vysoký stožár\cite{Rychetnik:Motory}\cite{ve:ve}.
		
		Pro svůj návrh jsem se rozhodl pro vztlakovou horizontální turbínu. Vztlakové turbíny mají vyšší účinnost, jsou použitelné pro vyšší rychloběžnosti a také jsou technicky zajímavější než odporové. Při volbě mezi svislou a horizontální turbínou jsem se po dlouhém zvažování rozhodl pro horizontální. To i přes fakt, že turbína bude umístěna v~zástavbě, kde je turbulentní okolí. Tudíž lze podle výše uvedeného usuzovat, že je vhodnější vertikální turbína.
		
		Vedlo mě k tomu několik faktů; Darrieus není sám o sobě schopný rozběhu. Je mu nutno dodat počáteční rotaci. U~malých turbín se tento nedostatek řeší pomocným, např. Savoniovým, rotorem, který ji rozběhne. O alternativním způsobu rozběhu Darrieovi turbíny pojednává práce \uv{Self-starting Darrieus Wind Turbine}\footnote{Práci lze nalézt na http://www.webalice.it/acecere48/finalreport.pdf} z univerzity Dalhousie. Zde jsou listy turbíny rozděleny na 2 části, které se mohou od sebe rozevírat – při rozběhu jsou rozložené a pracují v odporovém režimu. Při dosažení daných otáček se listy opět složí a pracují ve vztlakovém režimu. Toto řešení je zajímavé, avšak klade ještě větší výrobní nároky – již tak tenké a dlouhé listy je nutno rozpůlit.
		
		Pro horizontální turbínu však hlavně rozhodly mé předchozí pozitivní zkušenosti ze stavby a provozu tohoto typu turbíny.

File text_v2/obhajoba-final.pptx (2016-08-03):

## Návrh malé větrné turbíny

Jan Mrázek

## Cíle práce

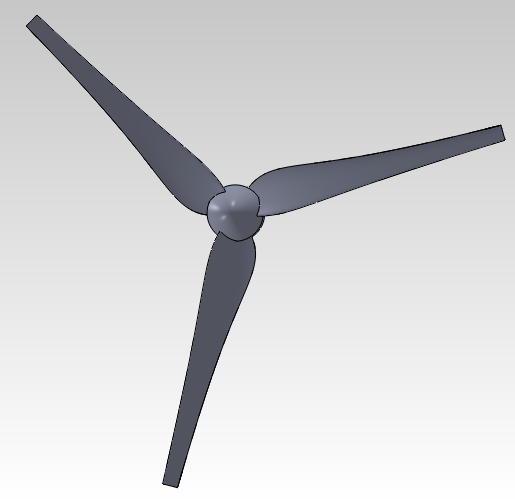
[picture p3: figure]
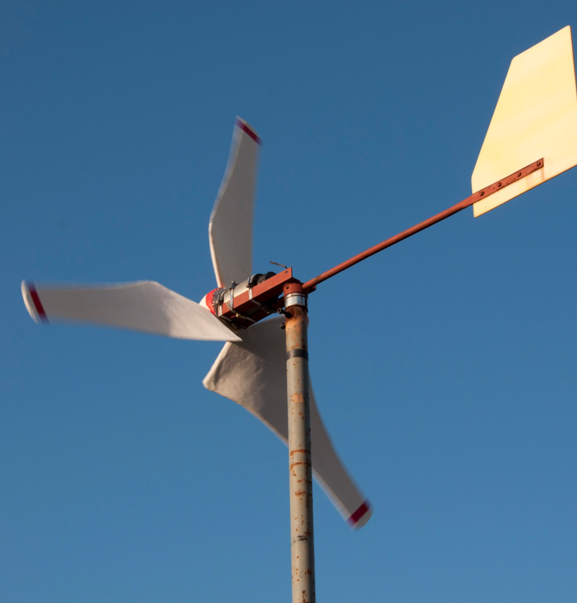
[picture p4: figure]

## Výběr turbíny

- Podle principu
  - Odporové
  - Vztlakové
- Rozdělení podle umístění osy rotace:
  - Horizontální
  - Vertikální

## Základní teorie

- Hlavním principem je určit směr ofukování aerodynamického profilu na rotoru
- Uvažuje 2 pohyby – pohyb proudu vzduchu (větru) a samotnou rotaci rotoru

## Rozšířená teorie

- Uvažuje třetí pohyb – vír vznikající za rotorem

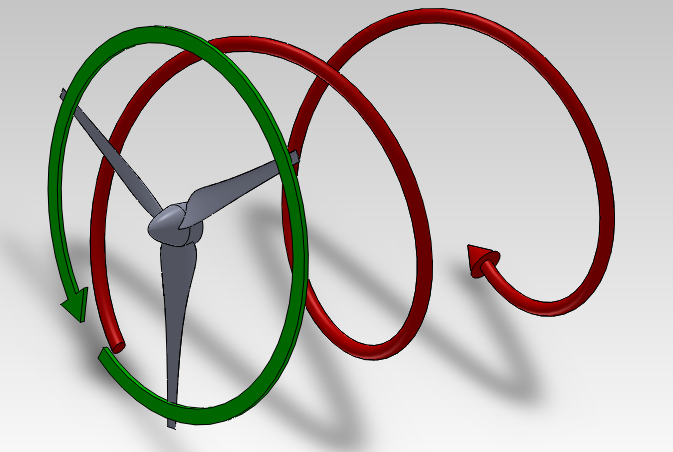
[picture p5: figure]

## Výpočet rozšířené teorie

- Pravděpodobně nelze řešit jinak než iteračně

## Parametry turbíny

- Pro turbínu byly zvoleny následující parametry:
  - Průměr 2,5 m
  - Neregulovaná (konstantní rychloběžnost)
  - Rychloběžnost 5
  - Tři listy

## Výběr profilu

- Zvolen profil SG6043 díky velkému rozsahu použitelných úhlů náběhu.

## Základní model listu

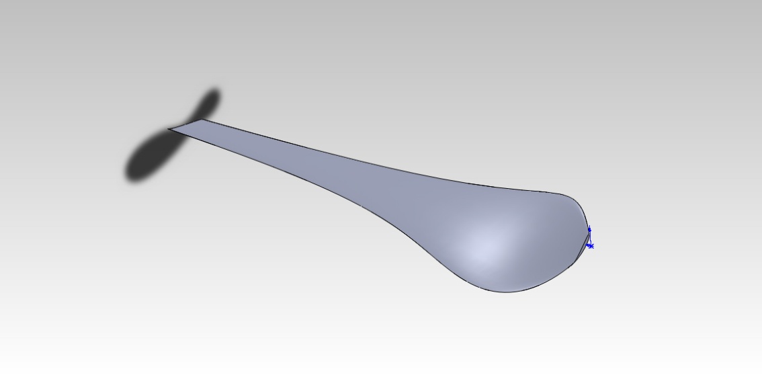
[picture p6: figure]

## Problematické oblasti

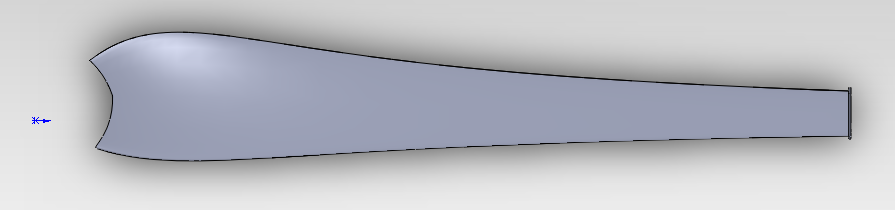
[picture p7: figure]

- Velká spotřeba materiálu za malý zisk energie
- Zlepšuje startovatelnost turbíny

Vznik indukovaných ztrát

## Výsledek simulací

- Osvědčilo se pětimilimetrové odsazení
- Ostatní zakončení mají potenciál, ale je u nich příliš mnoho parametrů

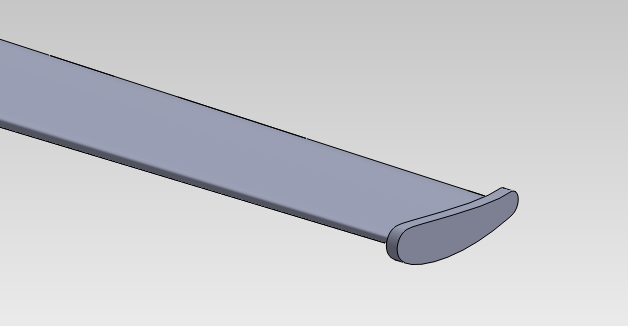
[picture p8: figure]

## Finální model

Rychlost větru | 5 ms⁻¹
Výkon vzduchu procházejícího turbínou | 441 W
Axiální síla | 69 N
Moment síly ohýbající list | 32 Nm
Síla roztáčející turbínu | 15 N
Krouticí moment | 11 Nm
Otáčky rotoru | 160 min⁻¹
Užitný výkon turbíny | 176 W (Cp = 40 %)

## Možnosti vylepšení návrhu

- Vylepšit zakončení listu:
  - Najít vhodné teoretické podklady
  - Realizovat iterační optimalizaci pomocí CFD simulace
- Najít profil, který
  - Dosahuje vyšší jemnosti na stejném nebo větším rozsahu náběhových úhlů
  - Má větší tloušťku
- Rozšířit teorie o další parametry (nestejnoměrné zpomalování vzduchu)

## První prototyp

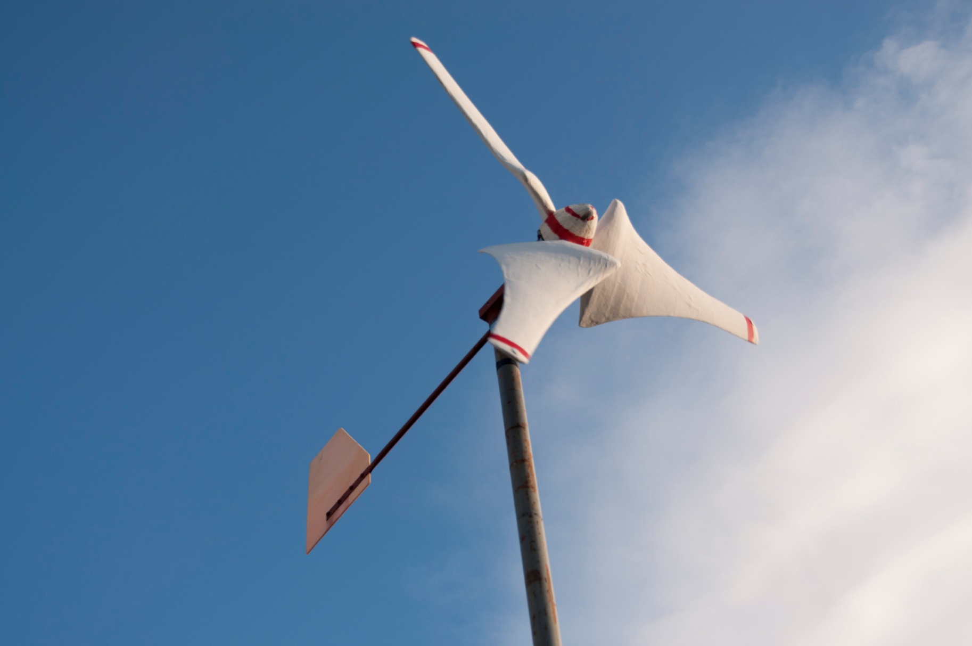
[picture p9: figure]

## První prototyp

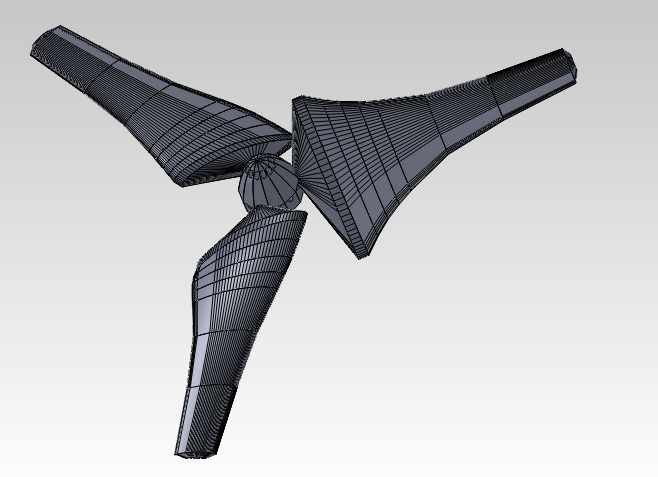
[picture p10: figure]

## Model listu

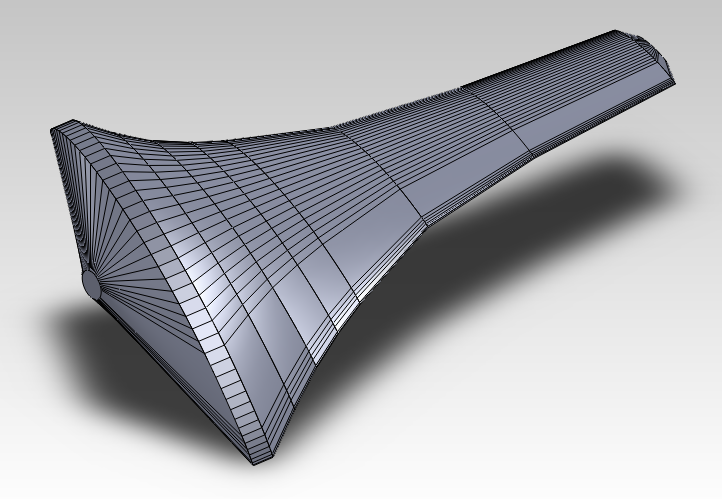
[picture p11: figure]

- Zde je patrná největší chyba – záměna tlakové a podtlakové strany

## První prototyp

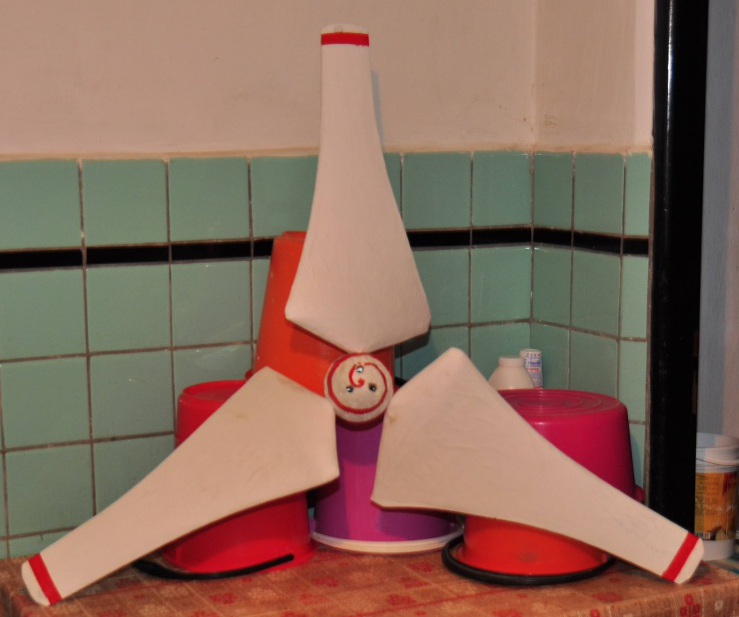
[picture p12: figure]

## První prototyp

## Zkušenosti s prvním prototypem

- Dobrá startovatelnost
- Tichost
- Osvědčila se výrobní technologie
- Nejsou na něj žádné stížnosti
- Nedodává téměř žádnou energii díky otočení profilu
- Dle simulace není zakončení listu ideální

## Cíle do budoucna

- Vyrobit zde navrženou turbínu
- Postavit nový, pevnější stožár
- Dokončit vývoj generátoru
- Dát dohromady novou gondolu se všemi bezpečnostními prvky (jak mechanickými, tak i elektronickými)
- Získanou energii využívat k topení
- Přidat telemetrii s webovým rozhraním

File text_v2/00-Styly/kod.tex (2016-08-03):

\usepackage{listings}
  \usepackage{courier}
 \lstset{
         basicstyle=\footnotesize\ttfamily, % Standardschrift
         %numbers=left,               % Ort der Zeilennummern
         numberstyle=\tiny,          % Stil der Zeilennummern
         %stepnumber=2,               % Abstand zwischen den Zeilennummern
         numbersep=5pt,              % Abstand der Nummern zum Text
         tabsize=2,                  % Groesse von Tabs
         extendedchars=true,         %
         breaklines=true,            % Zeilen werden Umgebrochen
         keywordstyle=\color{red},
    		frame=b,         
 %        keywordstyle=[1]\textbf,    % Stil der Keywords
 %        keywordstyle=[2]\textbf,    %
 %        keywordstyle=[3]\textbf,    %
 %        keywordstyle=[4]\textbf,   \sqrt{\sqrt{}} %
         stringstyle=\color{white}\ttfamily, % Farbe der String
         showspaces=false,           % Leerzeichen anzeigen ?
         showtabs=false,             % Tabs anzeigen ?
         xleftmargin=17pt,
         framexleftmargin=17pt,
         framexrightmargin=5pt,
         framexbottommargin=4pt,
         %backgroundcolor=\color{lightgray},
         showstringspaces=false      % Leerzeichen in Strings anzeigen ?        
 }
 \lstloadlanguages{% Check Dokumentation for further languages ...
         %[Visual]Basic
         %Pascal
         %C
         %C++
         %XML
         %HTML
         Java
 }
    %\DeclareCaptionFont{blue}{\color{blue}} 

  %\captionsetup[lstlisting]{singlelinecheck=false, labelfont={blue}, textfont={blue}}
  \usepackage{caption}
\DeclareCaptionFont{white}{\color{white}}
\DeclareCaptionFormat{listing}{\colorbox[cmyk]{0.43, 0.35, 0.35,0.01}{\parbox{\textwidth}{\hspace{15pt}#1#2#3}}}
\captionsetup[lstlisting]{format=listing,labelfont=white,textfont=white, singlelinecheck=false, margin=0pt, font={bf,footnotesize}}

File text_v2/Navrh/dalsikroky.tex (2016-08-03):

\chapter{Další kroky v návrhu}\label{chap:kroky}
V předchozí kapitole jsem vytvořil základní model rotorového listu. Tento list však má spoustu nevyjasněných prvků, které Gluertova teorie nepokrývá. V této kapitole bych se na ně chtěl zaměřit a probrat je.

\section{Oblast kolem středu, startovatelnost}
Ve většině konstrukcí amatérských větrných turbín si lze všimnout, že autoři záměrně vypouští část listu blízko osy otáčení. Např. v knize \cite{Crome:Technika} autoři vypouští polovinu poloměru. Obdobně i různí autoři uvedení v knize \cite{Hallenga:Elektrarna} vypouští oblast kolem středu.

Tato oblast je vypouštěna nejen díky nízkému výkonu (viz. graf \ref{graf.vykon}), ale také díky dlouhé tětivě, tudíž i větší spotřebě materiálu. Navíc profil v tomto místě omezuje nosnou konstrukci.
\begin{figure}[H]
	\centering
	
	\caption{Výkon jednotlivých elementů na poloměru $r$}
	\label{graf.vykon}
\end{figure}
V mém návrhu tuto oblast nevypouštím, jelikož se nejvíce podílí na startovatelnosti, která je v turbulentním prostředí důležitá. Na první pohled tato informace vypadá jako nesmysl – síla zde působí na krátké páce a vyvolává malý krouticí moment. Podstata startovatelnosti spočívá jinde.

Veškeré teorie uvažují konstantní rychloběžnost, která však při rozběhu rotoru nenastává. Rotor má menší (resp. nulové) otáčky díky čemuž se mění i směr relativní rychlosti proudu vzduchu a profil není ofukován pod optimálním úhlem, tudíž na něm nevzniká tak velký vztlak (naopak narůstá odpor). Tato odchylka se se vzrůstající rychloběžností zvětšuje. A právě v~oblasti blízko osy rotace je rychloběžnost jednotlivých elementů listu velmi malá, díky čemuž je i~odchylka od ideálního úhlu náběhu malá. K lepší startovatelnosti také významně pomáhá profil, který má charakteristiku podobnou grafu \ref{graf.jemnost1}. Profil je \uv{tolerantnější} k úhlu náběhu a podává dobré výsledky i při nekonstantní rychloběžnosti.

Jelikož má tato oblast listu relativně malou obvodovou rychlost $u$, nezpůsobí zde změna tvaru profilu příliš velký rozdíl v~jeho vlastnostech. Proto je výhodné v této oblasti zvýšit tloušťku profilu a získat více prostoru pro nosnou konstrukci. Tuto změnu tloušťky jsem však do mého CAD modelu zatím nezanesl – ještě nejsou přesně známy technické detaily ohledně realizace rotorových listů.

\section{Zakončení listů}
Gleurtova teorie, stejně jako i ostatní, přepokládají, že rotor má nekonečný počet nekonečně tenkých lopatek. V praxi se však ničemu takovému nelze přiblížit.

Malý počet lopatek se projevuje aerodynamickými ztrátami. Příčinu těchto ztrát lze vysvětlit rozdílným tlakem na tlakové a podtlakové straně aerodynamického profilu. Díky tomuto rozdílu se vzduch na konci listu \uv{přelévá} z tlakové strany na podtlakovou ve snaze tento rozdíl vyrovnat. Tím uděluje proudu vzduchu rotační složku a na konci lopatky tak vzniká tzv. indukovaný vír. Tento vír snižuje vztlakovou sílu na konci listu a je také jednou z příčin hlučnosti větrných turbín.

Nenašel jsem žádnou literaturu, která by se problémem indukovaných vírů u větrných turbín zabývala. Literaturu zabývající se snížením ztrát u křídel letadel lze najít, avšak není příliš podrobná. Většinou jsou v ní indukované víry pouze zmíněny a možnosti, jak je omezit, jsou uvedeny pouhým výčtem. Nenašel jsem nikde popis, jak má např. vypadat winglet, aby měl správnou funkci.

Rozhodl jsem se proto jít experimentální cestou. Jelikož jsou však praktické pokusy časově, materiálně a technicky náročné, rozhodl jsem se využít CFD simulace.

Nesnažil jsem se o odvození teorie, pouze jsem chtěl zjistit, jak lze list rotoru ukončit, aby se snížily indukované ztráty (a potenciálně i hlučnost). Připravil jsem si šest různých zakončení rotorového listu, která jsem následně otestoval v simulaci. Inspiraci pro tato zakončení jsem čerpal z různých zdrojů. Od křídel dopravních letadel, přes fotografie větrných elektráren až po RC modely.

Jako simulační software jsem použil studentskou verzi Autodesk Simulation Multiphysics. Původně jsem plánoval použít open-source projekt OpenFOAM\footnote{http://www.openfoam.com/}. Ten je na rozdíl od Autodesk Simulation komplexnější, více přizpůsobitelný, avšak jedná se spíše o C++ framework, než program pro koncového uživatele. OpenFOAM nemá žádné GUI, veškerý vstup se do něj zadává pomocí zdrojových kódů. Naučit se tento program používat je na dlouhou dobu. Proto jsem se rozhodl, že použiji uživatelky přívětivější Autodesk Simulation.

Jelikož jsou CFD simulace relativně početně náročné, neprováděl jsem je na celém listu. Simulace jsem prováděl na posledních 25 centimetrech listu. Zde se úhel náběhu již příliš nemění, a je tedy proto možné tento úsek ofukovat pod stejným úhlem bez velké změny na vlastnostech. To opět zjednodušuje simulaci.

Simulaci jsem prováděl v bounding-boxu o rozměrech 100 $\times$ 80 $\times$ 40 cm (délka za listem, prostor ve směru listu, prostor pod a nad listem). Tato oblast je relativně malá. Díky tomu výpočet neprobíhal příliš dlouho (zhruba hodinu). Ovšem jak ukázaly výsledky, tato oblast byla pro některá zakončení malá a výsledky byly ovlivněny stěnami bounding-boxu. Avšak pro mé účely, kdy nepotřebuji přesné hodnoty, pouze porovnávám několik případů, je tato nepřesnost opomenutelná.

Simulace jsem prováděl pro rychlost větru 5~$m\cdot s^{-1}$, konec listu jsem tedy ofukoval proudem vzduchu s rychlostí 25~$m\cdot s^{-1}$ (zanedbal jsem vektorový součet rychlostí). Byla použita simulace typu \uv{Unsteady fluid flow}, která je manuálem pro aerodynamické simulace doporučována. Simuloval jsem dobu 5 sekund, rozdělenou na 200 snímků. Pro počet iterací mezí jsem ponechal standardní hodnotu 15. Proud vzduchu byl spuštěn bez vzestupné rampy (tzn. od začátku simulace měl zadanou rychlost, rychlost byla po celou dobu konstantní).

První simulaci jsem provedl na prostém ukončení listu beze změn, abych měl s čím výsledky porovnávat. Na této simulaci jsem také zkoušel, jak porovnávat výsledky. Ukázalo se, že na znázornění rychlosti (obrázky \ref{sim:2} a \ref{sim:3}), ani grafech rychlosti jednotlivých bodů není nic poznat. Lehce průkazné bylo znázornění rychlosti ve směru osy X při pohledu zezadu na list (pohled proti směru proudícího vzduchu, obrázek \ref{sim:1}), kde lze vidět, jak se proud vzduchu pohybuje nad listem  na opačnou stranu než proud vzduchu pod listem. Avšak z tohoto znázornění lze pouze vyčíst existenci víru. Nelze určit jeho tvar, rychlost, ani jakou oblast listu ovlivňuje.

O víru toho nejvíce vypovídají proudnice. Proudnice jsou křivky, které mají v každém svém bodě směr rychlosti proudu vzduchu. Při pohledu zezadu listu (proti směru proudu vzduchu) je na nich jasně vidět vznikající vír, jeho velikost, pozice a rychlost. Z tohoto pohledu si lze vytvořit celkem jasnou představu o vznikajícím víru. Mírné doplnění poskytne i pohled shora, kde je vidět jak proudnice vybočují z rovnoběžného směru.

\begin{figure}[H]
	\centering
	
	\caption{Zde je vidět projev víru – červená barva znázorňuje pohyb vzduchu doleva, modrá doprava. Zelená barva značí nulovou rychlost.}
	\label{sim:1}
\end{figure}
\begin{figure}[H]
		\centering
		\subfigure[Velikosti rychlosti]{\label{sim:2}}~
		\subfigure[Velikosti rychlosti ve směru osy X]{\label{sim:3}}
		\caption{Neprůkazné znázornění výsledků}
	\end{figure}

Na obrázku \ref{sim:4} jsou zobrazeny výsledky simulace listu bez jakéhokoliv zakončení. Z proudnic na tomto obrázku lze jasně vypozorovat vír, který vzniká za listem. Jelikož se proudnice při pohledu zezadu jeví dlouhé, pohybuje se vír velkou úhlovou rychlostí.

Při podrobnějším zkoumání jsem si všiml, že víru jsou dva – velký na tlakové straně a menší na podtlakové. Velký vír také zasahuje více do oblasti samotného listu, naopak malý vír se nachází až za okrajem listu. Průměr velkého víru se pohybuje mezi 20–25~cm. Malý vír má průměr menší než 10~cm. Na proudnicích lze také vidět jasný tok vzduchu mezi tlakovou a~podtlakovou stanou.

Při pohledu shora si můžeme všimnout, že vír nejznatelněji ovlivňuje posledních 15~cm listu. Na opačnou stranu je koncem listu ovlivněn i vzduch 6~cm vzdálený od konce listu.

\begin{figure}[H]
	\centering
	
	\caption{Proudnice listu bez zakončení. Na obrázku vpravo je jasně patrný vír za listem. Na obrázku vlevo lze vidět, jak na konci listu přestávají být proudnice rovnoběžné.}
	\label{sim:4}
\end{figure}

\subsection{Zakončení odsazením}
Autor knihy \cite{Crome:Technika} používá na svých turbínách pro snížení indukovaného odporu přesah na konci listu. Tento přesah, respektive odsazení, má za cíl omezit, popř. i úplně zamezit, toku vzduchu mezi tlakovou a podtlakovou stranou. Toto odsazení má velikost 10 mm, avšak autor má na svém listu mnohem delší tětivu než já. Rozhodl jsem se proto nasimulovat dvě velikosti odsazení – 5 a 10~mm.

Na obrázku \ref{konec:1} si lze prohlédnout model pětimilimetrového odsazení, na kterém byla provedena simulace.
\begin{figure}[H]
	\centering
	
	\caption{Pětimilimetrové odsazení na konci listu}
	\label{konec:1}
\end{figure}

\begin{figure}[H]
	\centering
	
	\caption{Výsledky pětimilimetrového odsazení na konci listu}
	\label{sim:5}
\end{figure}
Přidání této malé plošky výrazně mění charakter vnikajícího víru, jak je patrné na obrázku \ref{sim:5}. Je vidět, že vzniká pouze jediný vír, není zde přímý tok vzduchu mezi tlakovou a podtlakovou stranou a~úhlová rychlost víru je mnohem menší než v~předchozím případě. Vír se také posunul směrem z~plochy listu a~méně ji ovlivňuje.

Vír, který vzniká v pravém dolním rohu simulace, je způsoben malým simulačním prostorem – proud vzduchu zde ovlivňují stěny.
Při pohledu shora je jasně patrné minimální zakřivení proudnic. Vír tedy velmi rychle zaniká – to je dáno nižší úhlovou rychlostí.

Jinak však vypadá situace pro desetimilimetrové odsazení (obrázek \ref{sim:6}). Zde vzniká v místě zakončení proud s velkou úhlovou rychlostí obklopen druhým proudem s nízkou rychlostí. Při trojrozměrném zobrazení je vidět, že tento pomalý vír velmi rychle zaniká, avšak vnitřní vír pokračuje dále.

\begin{figure}[H]
	\centering
	
	\caption{Výsledky desetimilimetrového odsazení na konci listu}
	\label{sim:6}
\end{figure}

Můj původní předpoklad, že délku velikost odsazení je nutno přizpůsobit délce tětivy, se ukázal jako správný. Simulace ukazuje, že pětimilimetrové odsazení pravděpodobně funguje. Díky víru s malou úhlovou rychlostí vznikají nízké ztráty a díky absenci oblasti, kde přetéká vzduch z~tlakové strany na podtlakovou, omezuje vznik hluku. Navíc výroba odsazení není technicky náročná.

\subsection{Zakončení wingletem}
Winglet je zahnutý konec křídla u letadla. Funguje na podobném principu jako odsazení – brání vzduchu proti přetékání mezi stranami aerodynamického profilu. Tím, že je však tvořen aerodynamickým profilem, vyvolává dodatečný vztlak. Poprvé byl v~praxi použit na letadle NASA \cite{winglet}.

Při použití wingletu jsem vycházel z toho, že list rotoru je jednak podobný křídlu letadla, ale také z toho, že na některých velkých větrných elektrárnách je použit. Lze ho najít také na některých typech lodních šroubů.

Bohužel jsem nenašel žádnou literaturu, která by se přímo návrhem wingletu dostatečně zabývala. Jeho tvar jsem sestavil na základě fotografií některých křídel letadel a velkých větrných elektráren. Avšak takovéto sestavení je značně nedostatečné.

Sestavil jsem 2 modely (obrázek~\ref{konec:2}) - jeden winglet zahnutý o $85\,^{\circ}$ a druhý o $65\,^{\circ}$. Winglet jsem nasměroval na podtlakovou stranu jako u křídla letadla. Winglet má stejný profil jako celý list. Délka tětivy se lineárně zmenšuje až na polovinu původní délky.

\begin{figure}[H]
	\centering
	
	\caption{Model wingletu}
	\label{konec:2}
\end{figure}
Od takto sestaveného modelu jsem nečekal žádné zázračné výsledky. Avšak výsledky mě překvapily – díky wingletu se odklonem $65\,^{\circ}$ vznikal za rotorem vír velkého průměru s velkou úhlovou rychlostí (obrázek \ref{sim:7}). Winglet dokonce silně ovlivňoval proud kolem celé délky simulované části profilu.

Winglet s odklonem $85\,^{\circ}$ vykazoval mnohem lepší výsledky (obrázek \ref{sim:8}) – vznikal téměř neznatelný vír s malou oblastí rychlého proudění vzduchu.

\begin{figure}[H]
	\centering
	
	\caption{Simulce wingletu s odklonem $65\,^{\circ}$. Je vidět velký vír s velkou úhlovou rychlostí.}
	\label{sim:7}
\end{figure}

\begin{figure}[H]
	\centering
	
	\caption{Simulace wingletu s odkolonem $85\,^{\circ}$. Tento wingletu vykazuje znatelně lepší výsledky než předchozí.}
	\label{sim:8}
\end{figure}
Tato simulace mě přesvědčila, že winglet je účinným řešením indukovaných ztrát, avšak také ukázala, jak choulostivá oblast zakončení listu je. I malá změna může výrazně omezit vznikající indukovaný vír, ale také jej může výrazně podpořit.

Ačkoliv jeden z mých modelů vykazoval dobré vlastnosti, rozhodl jsem se v tomto návrhu větrné turbíny winglety nepoužít. Jedná se o oblast s nejistými výsledky, které nemám nějak podložené. Avšak studium a experimenty s winglety neopouštím – rozhodně se nejedná o slepou uličku. Pouze je metoda pokusu a omylu značně neefektivní.

\subsection{Zakončení obloukem dozadu}

Na obrázku \ref{konec:3} se nachází zakončení listu obloukem dozadu. Jako inspiraci jsem si zde vzal zakončení křídel rychlostní RC modelů letadel. Toto zakončení se také často objevuje na koncích vrtulí letadel čí lodních šroubů určených pro velké rychlosti.

\begin{figure}[H]
	\centering
	
	\caption{Zakončení listu obloukem dozadu}
	\label{konec:3}
\end{figure}

Je důležité poznamenat, že tento oblouk je v rovině listu – není zahnutý. Bohužel však opět tento tvar nemám podložený teorií. I většina autorů výše uvedených modelů tvoří tato zakončení \uv{jen tak}.

Toto zakončení vytváří velký, ale relativně pomalý vír (obrázek \ref{sim:9}). Tento vír má podobné vlastnosti jako vír v případě odsazení. Na výsledcích simulace je vidět zrychlení víru, které je ovšem opět způsobeno působením stěn simulačního prostoru.

\begin{figure}[H]
	\centering
	
	\caption{Výsledky simulace zakončení obloukem dozadu}
	\label{sim:9}
\end{figure}

\subsection{Zakončení kopulí}
Na spoustě malých větrných elektráren lze vidět zakončení listu kopulí. Toto zakončení je často používáno i na křídlech letadel. Model zakončení kopulí je na obrázku \ref{konec:4}.

\begin{figure}[H]
	\centering
	
	\caption{Model zakončení listu obloukem}
	\label{konec:4}
\end{figure}

Od tohoto zakončení jsem očekával dobré výsledky – přece jen je hojně používané. Výsledky mě překvapily (obrázek~\ref{sim:10}). Na konci křídla vzniká velký vír s velkou úhlovou rychlostí. Pozitivem je, že tento vír nevzniká za aktivní plochou listu, tudíž jej příliš neovlivňuje.

\begin{figure}[H]
	\centering
	
	\caption{Výsledky simulace zakončení kopulí}
	\label{sim:10}
\end{figure}

Je však možné, že výhoda tohoto zakončení spočívá jinde. Díky tomu, že tečně navazuje na konec listu a jedná se o hladkou plochu bez ostrých hran, nevznikají na tomto zakončení chvění vzduchu způsobující hluk. Tuto domněnku však nemohu potvrdit – simulaci tohoto typu jsem nebyl schopen provést.

\subsection{Výběr zakončení}
Z výše uvedeného porovnání vyplývá, že dobré výsledky dává zakončení pětimilimetrovým odsazením, wingletem a obloukem dozadu.

Pro svůj model jsem použil odsazení, jelikož se jedná o tvar, ve kterém hraje roli jediná proměnná – velikost odsazení a ta jde jednoduše nasimulovat. Ostatní zakončení jsou komplexními tvary, které za některých okolností podávají dobré a za některých okolností špatné vlastnosti.

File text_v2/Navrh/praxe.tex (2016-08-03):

\chapter{Použití teoretických poznatků}\label{chap:praxe}
Tato kapitola přímo vychází z teorie vysvětlené v kapitole \ref{kap:teorie} a snaží se ji využít při návrhu větrné turbíny.

\section{Parametry návrhu}
V této podkapitole bych rád vytyčil cíle, respektive požadované parametry, navrhované větrné turbíny.

Jak jsem již zmínil v úvodu, čím menší větrná turbína, tím méně je ekonomicky rentabilní. Turbíny s průměrem menším než 5~metrů jsou v podstatě nerentabilní. Proto se v návrhu nebudu omezovat komplikovaností či finanční náročností výroby turbíny. Cílem je navrhnout co nejúčinnější turbínu, která může být umístěna v zástavbě a bude fungovat jako technická zajímavost.

Jelikož bude turbína umístěna v zástavbě, je nutné zvolit rozumnou velikost, aby nebyla příliš rušivá. Čím větší turbína, tím jsou také nižší otáčky při stejné rychloběžnosti. S velkou turbínou se také pojí vyšší zatížení stožáru, který pak musí být kotven např. pomocí lan, což je v zástavbě, resp. na zahrádce, značně omezující. Naopak i malý přírůstek na průměru přidá na výkonu turbíny – výkon turbíny je odvislý od její plochy, přičemž ta roste se čtvercem poloměru. Nakonec jsem se rozhodl pro návrh turbíny s průměrem 2,5~m. Vycházel jsem zde ze zkušeností s~prvním prototypem, jehož průměr 1,5~metru se ukázal jako malý a průměr turbíny přes 3~metry by mohl působit značně rušivě. Navíc již nyní se vyskytly problémy s~manipulací se sestavenou 1,5m turbínou.

Dalším charakteristickým znakem větrné turbíny je počet listů. Zde jsem zvolil 3. Toto číslo bylo zvoleno adekvátně k požadované rychloběžnosti dle tabulky na straně 70 v knize \cite{Rychetnik:Motory}. Navíc vzhled turbíny je „přirozený“ – většině lidí se pod pojmem větrná elektrárna vybaví právě třílistá turbína.

Posledním voleným parametrem turbíny je její rychloběžnost. U prvního prototypu byla zvolena relativně nízká rychloběžnost~4 díky obavám z hluku (při vyšší rychloběžnosti se konce listů pochybují rychle, čímž snadněji vyvolávají hluk). Obavy se ukázaly jako neopodstatněné. Podle grafu na stránkách \cite{ve:ve}\footnote{http://ve.ic.cz/files/teorie/ucinnost.png}  a tabulky 3.1 v knize \cite{Rychetnik:Motory}, leží maximální účinnost třílisté turbíny mezi rychloběžností 5 a 6. Jelikož požadavek na nízkou hlučnost je relativně důležitý, rozhodl jsem se pro jistotu zvolit rychloběžnost 5.

Jelikož není potřeba vytvářet síťové napětí, nebude mít turbína z důvodu jednoduchosti nastavitelné listy pro regulaci otáček. Tím se také zvýší její účinnost.

\section{Výběr profilu}
Prvním krokem při návrhu turbíny hned po stanovení jejích parametrů je výběr turbíny. Z~předchozí teorie vypadá, že stačí vybrat pouze profil s co největším poměrem součinitelů $c_y/c_x$. Výběr profilu však má některá úskalí, která bych v této kapitole chtěl probrat.

\subsection{Reynoldsovo číslo}
V kapitole \ref{kap:zakladprinc} jsem zmínil, že aerodynamické vlastnosti profilu souvisí s podmínkami, ve kterým je provozován. Tyto podmínky charakterizuje Reynoldsdovo číslo \cite{Rychetnik:Motory}, která bylo definováno v rovnici \eqref{rov:13}.

Jedná se pouze o orientační údaj; vlastnosti profilů se na jeho velikosti mění pouze málo. Např. pro profil SG6043 je součinitel $c_y$ pro $Re$ $10^5$ roven 1,415; pro $7,5\cdot 10^4$ 1,408 a pro $5\cdot 10^4$ je 1,389. Tato data byla převzata z \cite{profil}\footnote{http://www.worldofkrauss.com/foils/getpolar/787.dat}. Navíc parametry profilů jsou dostupné pouze pro některá Re.
Abych mohl spočítat $Re$, je nutné odhadnout délku tětivy. Její délka se však výrazně mění. Většinou se však uvažuje délka tětivy u konce listu, která má největší podíl na výkonu. Délka tětivy se v tomto případě pohybuje okolo 10~cm.

Také rychlost obtékání profilu se uvažuje pouze jako obvodová rychlost rotoru, nikoliv jako vektorový součin obvodové rychlosti rotoru a rychlosti větru. Pro vítr o rychlosti 4 $m\cdot s^{-1}$ je~$Re$ \eqref{rov:50}:
\begin{equation}
	\label{rov:50}
	Re=\frac{vl}{\nu}=\frac{v_1\cdot\lambda l}{\nu}=\frac{4\cdot 5 \cdot 0,1}{15\cdot 10^6}\doteq 1,33\cdot 10^5
	\end{equation}
Je tedy nutné vybírat z profilů, které vykazují dobré vlastnosti při $Re$ $1,33\cdot 10^5$.

\subsection{Ideální vlastnosti profilu}
V~tabulkách k~daným profilům, lze zpravidla najít údaj o maximální hodnotě poměru $c_y/c_x$ (též označovaného jako jemnost profilu). Z~čistě teoretického hlediska lze říci, že tento parametr je dostačující.

V praxi však nelze dosáhnout ideálních podmínek. Všechny teorie uvedené v předchozí kapitole předpokládají, že směr relativní rychlosti větru $\beta$ je konstantní. V praxi to však nelze dodržet. Zpravidla nastávají tři nepříznivé situace:
\paragraph{Vítr nevane v celé ploše turbíny stejnou rychlostí.} Tento jev se projevuje hlavně u~velkých turbín. Avšak má vliv i na malé turbíny, zejména v turbulentním prostředí, kde jsou rozdíly rychlostí velké. Zástavba takovým prostředím bezpochyby je.
\paragraph{Turbína je zatížena.} Při přílišném zatížení turbíny se sníží její rychlost otáčení, což vede ke snížení rychloběžnosti a změně směru relativní rychlosti větru.
\paragraph{Turbína se rozbíhá.} Při rozběhu se turbína otáčí pomaleji než je navržena, tudíž její rychloběžnost opět není konstantní a relativní proud vzduchu má opět jiný směr než ideální.\vspace{0.5cm}

Z těchto důvodů je vhodné, aby profil měl co nejpodobnější hodnoty součinitelů $c_x$ a $c_y$ pro co největší rozsah úhlů náběhu – díky tomu bude turbína podávat dobré vlastnosti i při nepříznivých podmínkách. Je také výhodné, aby maximální hodnota jemnosti profilu měla podobné hodnoty od sebe jak v~kladném, tak i záporném směru – důvod je zřejmý. Na grafech \ref{graf.jemnost1}, \ref{graf:jemnost2} a \ref{graf:jemnost3} jsou zobrazeny ilustrační příklady takových průběhů jemnosti profilu.

\begin{figure}[H]
	\centering
	
	\caption{Graf zobrazuje vhodný průběh jemnosti profilu k úhlu náběhu. Je vidět, že profil dává v~rozmězí $2$–$8\,^{\circ}$ velmi podobné výsledky. Data jsou pouze ilustrační, nejsou založena na žádném existujícím profilu}
	\label{graf.jemnost1}
\end{figure}

	\begin{figure}[H]
	\centering
	\subfigure[Maximálních hodnot jemnosti profil dosahuje pouze na minimálním úseku]{\label{graf:jemnost2}}~
	\subfigure[Charakteristika je výrazně asymetrická]{\label{graf:jemnost3}}
	\caption{Grafy znázorňují nevhodný průběh jemnosti profilu. Data jsou pouze ilustrační.}
	\end{figure}
	
\subsection{Výběr profilu}
	Ze stránek Airfoil Inverstigation Database \cite{profil} jsem vybral několik na první pohled vhodných profilů. A to profily WORTMANN FX 60-126, EPPLER 395, GOE 481A a SG6043. V této kapitole je na základě výše uvedených kritérií porovnám. Veškerá data o profilech jsou převzata také z těchto stránek.
	\paragraph{WORTMANN FX 60-126}(obrázek \ref{profil:wort}) Tento profil na první pohled zaujme vysokou jemností profilu (graf \ref{profil:wortj}) – 170 při úhlu náběhu $5\,^{\circ}$. Avšak při pohled na průběh jemnosti je jasné, že tento profil není vhodný do nepříznivých podmínek – ideálních hodnot dosahuje pouze na malém intervalu úhlů náběhu, navíc asymetricky.
	\begin{figure}[H]
		\centering
		
		\caption{Profil WORTMANN FX 60-126}
		\label{profil:wort}
	\end{figure}
	\begin{figure}[H]
			\centering
			
			\caption{Jemnost profilu WORTMANN FX 60-126}
			\label{profil:wortj}
	\end{figure}
	\paragraph{EPPLER 395} (obrázek \ref{profil:epp}) Tento profil opět na první pohled lákal vysou jemností (graf \ref{profil:eppj}) – 80. Směrem do záporných hodnot jeho jemnost klesá pozvolna, avšak do kladných prudce klesá. Pro mé podmínky se jedná o nevhodný profil.
	\begin{figure}[H]
			\centering
			
			\caption{Profil EPPLER 395}
			\label{profil:epp}
		\end{figure}
		\begin{figure}[H]
				\centering
				
				\caption{Jemnost profilu EPPLER 395}
				\label{profil:eppj}
		\end{figure}
	\paragraph{GOE481A} (obrázek \ref{profil:goe}) Tento profil dosahuje jemnosti 73 a tuto vysokou jemnost udržuje na dlouhém intervalu úhlů náběhu – od 3 do $8\,^{\circ}$ (graf \ref{profil:goej}). Má i relativně velkou tloušťku, což je výhodné pro konstrukci listu.
	\begin{figure}[H]
			\centering
			
			\caption{Profil GOE481A}
			\label{profil:goe}
		\end{figure}
		\begin{figure}[H]
				\centering
				
				\caption{Jemnost profilu GOE481A}
				\label{profil:goej}
		\end{figure}
		
	\paragraph{SG6043} (obrázek \ref{profil:sg}) Tento profil podobně jako GOE481A dosahuje jemnosti 70 a drží si ji na podobném intervalu (graf \ref{profil:sgj}). Oproti němu však tyto hodnoty nekolísají, což je výhodné. Jeho nevýhodou v porovnání s GOE481A je menší tloušťka.
		\begin{figure}[H]
				\centering
				
				\caption{Profil SG6043}
				\label{profil:sg}
			\end{figure}
			\begin{figure}[H]
					\centering
					
					\caption{Jemnost profilu SG6043}
					\label{profil:sgj}
			\end{figure}
	
	Z těchto profilů se ukázaly jako vhodné pouze 2; a to GOE481A a SG6043. Po zvážení jsem se rozhodl pro SG6043. Jednak má plynulejší průběh jemnosti a navíc s~ním mám už předchozí pozitivní zkušenosti
	
	\section{Postup výpočtu}\label{postup}
	V kapitole \ref{kap:funkce2} jsem zmínil, že výpočet podle Glauerta nelze řešit klasicky. V této kapitole bych rád vysvětlil jednak proč jej nelze řešit klasicky, ale hlavně také jak jej vyřešit.
	
	Při prvním pohledu na problematiku si lze všimnou koeficientů $h$ a $k$, které nejsou nějak definovány. Vystupují jako vstupní hodnota. Tyto koeficienty mohou nebývat nekonečně mnoha platných hodnot. Nás však zajímá hodnota, pro kterou dávají maximální výkon. Je proto vhodné zavést tzv. součinitel výkonu $C_p$ \eqref{rov:51}, který charakterizuje účinnost elementu turbíny na daném poloměru \cite{Rychetnik:Motory}.
	\begin{equation}
		\label{rov:51}
		C_p=\frac{\mathrm{d}P_{turbíny}}{\mathrm{d}P_{vzduchu}}=\frac{\omega\;\mathrm{d}M}{\rho\pi r \; \mathrm{d}rv_1^3}=\frac{\omega^2r^2(1+k)(h-1)}{v_1^2}=\lambda_r^2(1+k)(h-1)
	\end{equation}
	Z této definice by se mohlo zdát, že maximální výkon je nekonečně velký, nesmíme však zapomínat, že součinitelé $k$ a $h$ mají mezi sebou vztah. Tento vztah vychází z~výpočtu úhlu $\beta$ (rovnice \eqref{rov:36}). Pokud tento vztah dosadíme do výsledné rovnice teorie podle Glauerta (rovnice \eqref{rov:49}), získáme vztah \eqref{rov:52}.
		\begin{equation}
			\label{rov:52}
			k= 1 - \lambda_r(h-1)\cot(\beta-\varepsilon)
		\end{equation}
	Z těchto vztahů je patrná cyklická závislost – např. $\beta$ závisí na $k$ a $h$, přičemž $k$ závisí na $\beta$. Koeficient $k$ vychází z~neznámého koeficientu $h$ atd.
	
	Výpočet této soustavy lze provést pouze iteračně. Ručně je takovýto výpočet prakticky neproveditelný, ale na počítači je to otázka zlomků sekund.
	
	Než popíši postup výpočtu, rád bych zmínil ještě jeden poznatek patrný z výše uvedených vztahů. Koeficienty, potažmo i výkonový součinitel, vychází z~rychloběžnosti na poloměru $r$, nikoliv z~rychloběžnosti na konci lopatek. Tudíž budou tyto koeficienty na různých poloměrech různé. Z~tohoto poznatku také plyne to, že nelze sestavit parametrickou rovnici např. pro délku tětivy v~závislosti na poloměru, která by šla zadat přímo do CAD programu. Jednotlivé body této rovnice se totiž opět musí počítat iteračně.
	
	Postup výpočtu jsem zvolil následující. Z rovnice \eqref{rov:51} vyplývá, že $h > 1$, protože proud vzduchu je zpomalován, nikoliv urychlován (tedy $k > 0$) a součinitel výkonu musí být kladný. Pro výpočet je nutné odhadnou výchozí hodnoty. Pro koeficient $k$ jsem vybral výchozí hodnotu $\frac{1}{3}$ podle Betzovy účinnosti. Jelikož jsem se rozhodl iterovat podle $h$, zvolil jsem hodnotu blízkou~1, která je dostatečné malá, aby mohla dále růst a nebyla za maximem součinitele výkonu. Konkrétně $1 + 10^{-5}$.
	
	Z těchto koeficientů vypočítám podle rovnice \eqref{rov:36} úhel $\beta$. Následuje první krok iterace, kdy z~vypočteného úhlu vypočítám podle rovnice \eqref{rov:52} novou hodnotu koeficientu $k$. Z této hodnoty opět vypočítám úhel $\beta$, a tak dále. Tento výpočet opakuji tak dlouho, dokud není rozdíl dvou po sobě jdoucích výsledků menší, než zadaná přesnost.
	
	Až získám přesné hodnoty koeficientu $k$ a úhlu $\beta$ pro danou hodnotu koeficientu $h$, vypočtu součinitel výkonu. Pokud je větší než předchozí, inkrementuji koeficient $h$ o daný inkrement. Pokud je vypočtená hodnota menší, snížím koeficient $h$ o daný inkrement. Pokud má změna součinitele výkonu opačný směr než předcházející, snížím hodnotu inkrementu. Poté znovu začnu určovat hodnotu úhlu $\beta$ a koeficientu $k$, tentokrát však pro novou hodnotu $h$.
	
	Tento postup opakuji do té doby, než inkrement klesne pod zadanou hodnotu (přesnost výpočtu).
	
	Na provedení tohoto výpočtu jsem napsal jednoduchý konzolový program v jazyce C++. Bylo by jej možné napsat i v jiných jazycích, ale C++ je mi nejbližší. Zdrojový kód programu je přiložen v příloze (program je však rozšířen o další funkcionalitu – viz dále). Program byl zamýšlen jako jednoúčelový, na jedno použití. Z toho důvodu program nepřebírá žádný uživatelský vstup a veškerá vstupní data jsou zadávána přímo do zdrojového kódu.
	
	\section{Tvorba CAD modelu}\label{kap:model}
	Předchozí kapitoly shrnují, jak zjistit jednotlivé parametry turbíny, ale neposkytují informace o jejich použití. Tato kapitola popisuje, jak jsem ze získaných dat sestavil základní CAD model turbíny.
	
	CAD model jsem vytvořil v programu SolidWorks, jehož studentskou verzi používám. Model by šel obdobně vytvořit~i~v~ostatních programech.
	
	Základní model jsem vytvořil pomocí funkce \uv{přidat tažením po křivce}, kde jsem táhl aerodynamický profil po přímce za pomoci dvou vodících křivek – jedna běží po náběžné hraně, druhá běží po odtokové hraně.
	
	Z grafů \ref{graf.glauert1} a \ref{graf.glauert2} vyplývá, že křivka není žádnou \uv{běžnou} – nejedná se kružnici, parabolu, či hyperbolu. Pro křivku také dle předchozí kapitoly není možné sestavit parametrickou rovnici, která by se dala přímo zadat do SolidWorks. Jedinou možností je pro tuto křivku určit dostatečné množství bodů a naimportovat ji do SolidWorks. Ten z~těchto bodů následně křivku pomocí splajnu zrekonstruuje.
	
	Pro generování bodů křivky jsem upravil program zmíněný v předchozí kapitole. Program generuje textový sobor, kde jsou tabulátorem oddělené hodnoty zarovnané do sloupců. Tento formát jsem zvolil pro jeho širokou podporu – dá se přímo importovat jak do SolidWorks, tak i~např. do Microsoft Excelu a jiných.
	
	Prvním krokem bylo určení orientace listu v prostoru. Abych respektoval předvolené názvy základních rovin v SolidWorks (přední, pravá a horní), je list umístěn následovně. Z počátku souřadnic, ve směru osy X, vybíhá poloměr. Profil listu je umístěn v rovině YZ, s tím, že osa Y je umístěna proti směru větru.
	
	\begin{figure}[H]
			\centering
			
			\caption{Umístění profilu v souřadném systému CAD programu.}
			\label{obr.profilosy}
		\end{figure}
	Z obrázku \ref{obr.profilosy} je patrné, jak lze spočítat souřadnice křivky pro náběžnou a odtokovou hranu. Náběžná hrana je křivka s body ve formátu [$r$, $y_1$, $z_1$], odtoková pak [$r$, $y_2$, $z_2$]. Výpočet těchto vzdáleností ukazují vztahy \eqref{rov:53}.
	\begin{eqnarray}
		\label{rov:53}
		y_1=bq\sin(\beta-\alpha) \nonumber \\
		z_1=bq\cos(\beta-\alpha) \nonumber \\
		y_2=b(q-1)\sin(\beta-\alpha)\nonumber \\
		z_2=b(q-1)\cos(\beta-\alpha)
	\end{eqnarray}
	Kde $b$ je délka tětivy, $\beta$ je úhel, který svírá směr relativního proud vzduchu s rovinou rotoru, $\alpha$ je úhel optimálního náběhu daného profilu a $q$ je koeficient vzdálenosti, ve které má profil největší tloušťku. Ten je zde proto, aby se profil v průběhu listu otáčel v místě s největší tloušťkou – cílem je získat co nejvíce prostoru na nosník.
	
	Tato úvaha však má jeden nedostatek – bod, okolo kterého se profil otáčí, neleží uprostřed profilu, ale na jeho tlakové hraně. Je proto nutné ho posunout o polovinu tloušťky profilu ve směru kolmém na tětivu. Tato úprava vypadá následovně\eqref{rov:54}.
	
	\begin{eqnarray}
		\label{rov:54}
		y_1=bq\sin(\beta-\alpha)+\frac{1}{2}bt\cos(\beta-\alpha) \nonumber \\
		z_1=bq\cos(\beta-\alpha)-\frac{1}{2}bt\sin(\beta-\alpha) \nonumber \\
		y_2=b(q-1)\sin(\beta-\alpha)+\frac{1}{2}bt\cos(\beta-\alpha)\nonumber \\
		y_2=b(q-1)\cos(\beta-\alpha)-\frac{1}{2}bt\sin(\beta-\alpha)
	\end{eqnarray}
	Kde $t$ je tloušťka profilu v~procentech délky tětivy profilu.
	Pro profil SG6043 je koeficient $q$~roven 0,33 a koeficient $t$~0,1 (patrno z tvaru tohoto profilu).  Použitím takto vypočtených křivek náběžné a odtokové hrany v prvku \uv{přidat tažením po křivce} vznikne následující model listu, potažmo celého rotoru (obrázky \ref{obr.model1} až \ref{obr.model3}).
	
	\begin{figure}[H]
				\centering
				
				\caption{Celkový pohled na rotorový list.}
				\label{obr.model1}
	\end{figure}
	
	\begin{figure}[H]
					\centering
					
					\caption{Pohled na list kolmo na pravou rovinu. Je zde patrný různý úhel náběhu a délka tětivy.}
					\label{obr.model2}
		\end{figure}
	\begin{figure}[H]
					\centering
					
					\caption{Pohled na celou turbínu složenou pouze ze 3 listů.}
					\label{obr.model3}
		\end{figure}
		
	\section{Parametry turbíny}
	Výše vytvořený model je teprve začátek návrhu. Potřebuje ještě několik úprav. Před jejich provedením bych však ještě rád uvedl parametry takto navržené turbíny.
	
	Data shrnuji v následujících třech tabulkách. Jsou vypočtena pro rychlosti větru 5~$m\cdot s^{-1}$ (tabulka \ref{tab:r5}), 10~$m\cdot s^{-1}$ (tabulka \ref{tab:r10}) a 25~$m\cdot s^{-1}$ (tabulka \ref{tab:r25}), což dle Beaufortovy stupnice odpovídá mírnému větru, čerstvému větru a vichřici.
	
	Data byla vypočtena pomocí tabulky v Microsoft Excelu pro jednotlivé elementy listu o~tloušťce 6,25~mm. Následně byly tyto hodnoty sečteny. Veškeré vztahy pro výpočet daných hodnot jsou uvedeny v kapitole \ref{kap:funkce2}. Hodnoty v~tabulkách jsou zaokrouhleny na celá čísla.
	\begin{table}[H]
		\centering
		\begin{tabular}{|l|l|}
		\hline
		Rychlost větru	&	5~$m\cdot s^{-1}$\\ \hline \hline
		Výkon vzduchu procházejícího turbínou	&441 $W$\\ \hline
		Axiální síla	&	69 $N$\\\hline
		Moment síly ohýbající list	&	32 $N\cdot m$\\\hline
		Síla roztáčející turbínu	&	15 $N$\\\hline
		Krouticí moment	&	11 $N\cdot m$\\\hline
		Otáčky rotoru	&	160 $min^{-1}$\\\hline
		Užitný výkon turbíny	&	176 $W$\\\hline	
		\end{tabular}
		\caption{Tabulka parametrů trurbíny pro rychlost 5~$m\cdot s^{-1}$}\label{tab:r5}
	\end{table}

		\begin{table}[H]
				\centering
				\begin{tabular}{|l|l|}
				\hline
				Rychlost větru	&	25~$m\cdot s^{-1}$\\ \hline \hline
				Výkon vzduchu procházejícího turbínou	&55 223 $W$\\ \hline
				Axiální síla	&1 734 $N$\\\hline
				Moment síly ohýbající list	&	481 $N\cdot m$\\\hline
				Síla roztáčející turbínu	&	390 $N$\\\hline
				Krouticí moment	&	262 $N\cdot m$\\\hline
				Otáčky rotoru	&	796 $min^{-1}$\\\hline
				Užitný výkon turbíny	&21 796 $W$\\\hline	
				\end{tabular}
				\caption{Tabulka parametrů trurbíny pro rychlost 25~$m\cdot s^{-1}$}\label{tab:r25}
			\end{table}
	
	Z těchto dat údajů si lze udělat představu jednak o podávaném výkonu a účinnosti, ale také hlavně o technických požadavcích na celou konstrukci. Je důležité si povšimnout, jak velká je síla působící na uložení, tedy i na stožár, a jak prudce roste. Stejně tak roste síla, která působí na list a ohýbá ho, potažmo ho vylamuje~z uložení v náboji. Všechny tyto parametry rostou s~třetí mocninou rychlosti větru. Důležité je uvažovat i působení odstředivé síly na listy, která roste \uv{pouze} s~druhou mocninou rychlosti větru. Tu však nelze spočítat, jelikož není známa konstrukce, a tudíž i hmotnost listu.
	
	Z těchto tabulek také vyplývá fakt, že turbína nutně potřebuje regulační zařízení, které ji při silném větru odstaví z~provozu. Reálný a bezpečný provoz je možný pouze pro rychlosti větru do 10–13~$m\cdot s^{-1}$.

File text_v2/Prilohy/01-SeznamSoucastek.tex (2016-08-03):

\chapter{Seznam použitých součástek}

Zde sepsaný seznam součástek je pouze orientační pro stavbu nové mlžné komory shodné s mnou postavenou. Na tu byly použity položky z tohoto seznamu. Ne všechny ale byly nově zakoupené, například zdroj, chladič a mnohé jiné pocházely ze starších počítačů, z mých předchozích experimentů apod. Celkové náklady na stavbu mlžné komory tedy byly mnohem menší. Uvedené ceny jsou při zakoupení nových dílů zjištěné k 2.~říjnu~2010.

\begin{table}[h]
	\centering
	\caption{Seznam součástek použitých při stavbě mlžné komory.}
	\label{tab:SeznamSoucastek:Komora}
	\begin{tabular}[t]{|r@{$\,$}l|p{4.6cm}|p{4.2cm}|p{3.1cm}|r@{$\,$}l|}
		\hline
		$ 1 $ & $\mathrm{l} $ & isopropanol												&	\href{http://www.ges.cz/-izoprop-1l-ges08000029.html}{IZOPROP 1L}																		&	\href{http://www.ges.cz}{GES Electronics}								&	$ 189 $ & $\textrm{Kč} $	\\
		$ 1 $ & $\mathrm{ks} $ & chladič 													&	\href{http://www.alza.cz/chladic-arctic-freezer-64-d56766.htm}{ARCTIC Freezer 64 PRO}									&	\href{http://www.alza.cz}{alza.cz}												&	$ 443 $ & $\textrm{Kč} $	\\
		$ 1 $ & $\mathrm{ks} $ & peltierův článek $ 51 \, \mathrm{W} $	&	\href{http://www.gme.cz/cz/m-tec1-12706-p601-017.html}{M-TEC1-12706}														&	\href{http://www.gme.cz}{GM Electronic}									&	$ 155 $ & $\textrm{Kč} $	\\	
		$ 1 $ & $\mathrm{ks} $ & peltierův článek $ 89 \, \mathrm{W} $	&	\href{http://www.gme.cz/cz/m-tec1-12710-p601-012.html}{M-TEC1-12710}														&	\href{http://www.gme.cz}{GM Electronic}									&	$ 177 $ & $\textrm{Kč} $	\\	
		$ 25 $ & $\mathrm{g} $ & teplovodivá pasta									&	\href{http://www.gme.cz/cz/pasta-teplovodiva-dc-se4490-cv-p749-069.html}{DC SE4490 CV}							&	\href{http://www.gme.cz}{GM Electronic}									&	$ 230 $ & $\textrm{Kč} $	\\	
		$ 2 $ & $\mathrm{ks} $ &LED modul												&	\href{http://www.gme.cz/cz/led-modul-vodotesny-5x-autoled-bila-78x18-mm-p960-164.html}{LED modul vodotěsný 5x autoled, bílá, 78x18 mm}			&	\href{http://www.gme.cz}{GM Electronic}			&	$ 24 $ & $\textrm{Kč} $	\\	
		$ 1 $ & $\mathrm{m} $ & odporový drát											&	\href{http://www.gme.cz/cz/rg-odp-kan01-p653-005.html}{RG-ODP-KAN01}														&	\href{http://www.gme.cz}{GM Electronic}									&	$ 22 $ & $\textrm{Kč} $	\\	
		$ 1 $ & $\mathrm{m} $ & rezistor $ 3,3 \, \mathrm{\Omega} $		&	\href{http://www.gme.cz/cz/rr-w10-3-3r-p114-186.html}{RR W10-3.3R}																	&	\href{http://www.gme.cz}{GM Electronic}									&	$ 10 $ & $\textrm{Kč} $	\\	
		$ 1 $ & $\mathrm{m} $ &smršťovací bužírka									&	\href{http://www.gme.cz/cz/f0920hs-15-bk-p656-467.html}{F0920HS-15 BK}															&	\href{http://www.gme.cz}{GM Electronic}								&	$ 6 $ & $\textrm{Kč} $	\\	
		$ 1 $ & $\mathrm{m} $ &smršťovací bužírka									&	\href{http://www.gme.cz/cz/f0920hs-20-p656-073.html}{F0920HS-20}																	&	\href{http://www.gme.cz}{GM Electronic}								&	$ 3 $ & $\textrm{Kč} $	\\	
		$ 1 $ & $\mathrm{ks} $ & box $ 1,1 \, \mathrm{l} $							&	TS VZDUCH. DOZA 1.1l																																					&	Tesco																							&	$ 60 $ & $\textrm{Kč} $	\\	
		$ 1 $ & $\mathrm{ks} $ & box $ 2,4 \, \mathrm{l} $							&	TS VZDUCH. DOZA 2.4l																																					&	Tesco																							&	$ 110 $ & $\textrm{Kč} $	\\	
		$ 1 $ & $\mathrm{ks} $ & hliníkový tácek											&	AL. TACEK 43$\times$28cm 1ks																																	&	Tesco																							&	$ 30 $ & $\textrm{Kč} $	\\	
		$ 1 $ & $\mathrm{ks} $ &houbička													&	houbička na nádobí																																								&	Tesco																							&	$ 5 $ & $\textrm{Kč} $	\\	
		$ 1 $ & $\mathrm{ks} $ & fólie																&	fólie A4																																													&	Tesco																							&	$ 2 $ & $\textrm{Kč} $	\\	
		$ 1 $ & $\mathrm{ks} $ & závitová tyč	 											&	závitová tyč $ 6 \, \mathrm{mm} $																																		&	 Železářství Lamex																	&	$ 6 $ & $\textrm{Kč} $	\\	
					&					 & šroubky, podložky, matky 							&																																																		& Železářství Lamex																		&	$ 40 $ & $\textrm{Kč} $	\\	
		\hline\hline
		\multicolumn{5}{|l|}{\textbf{Celkem}} & $ 1\,533 $ & $ \textrm{Kč} $ \\
		\hline
	\end{tabular}
\end{table}

\begin{table}[h]
	\centering
	\caption{Seznam součástek použitých pro stavbu zdroje.}
	\label{tab:SeznamSoucastek:Zdroj}
	\begin{tabular}[t]{|r@{$\,$}l|p{4.6cm}|p{4.2cm}|p{3.1cm}|r@{$\,$}l|}
		\hline
		$ 1 $ & $\mathrm{ks} $ & zdroj 													&	\href{http://www.alza.cz/zdroj-eurocase-350w-i-d44296.htm}{EUROCASE 350W PFC}											&	\href{http://www.alza.cz}{alza.cz}													&	$ 467 $ & $\textrm{Kč} $	\\
		$ 1 $ & $\mathrm{ks} $ & ventilátor 												&	\href{http://www.alza.cz/ventilator-primecooler-pc-8025l12c-d53092.htm}{PrimeCooler 8025L12C}			&	\href{http://www.alza.cz}{alza.cz}													&	$ 95 $ & $\textrm{Kč} $	\\
		$ 1 $ & $\mathrm{ks} $ & přístrojová krabička								&	\href{http://www.ges.cz/-kp-17-ges07203821.html}{KP 17}																							&	\href{http://www.ges.cz}{GES Electronics}									&	$ 52 $ & $\textrm{Kč} $	\\
		$ 1 $ & $\mathrm{m} $ & smršťovací bužírka							&	\href{http://www.ges.cz/-rc-160-ges06900482.html}{RC 1.6/0}																							&	\href{http://www.ges.cz}{GES Electronics}									&	$ 7 $ & $\textrm{Kč} $	\\
		$ 1 $ & $\mathrm{m} $ & smršťovací bužírka							&	\href{http://www.ges.cz/-rc-242-ges06900542.html}{RC 2.4/2}																							&	\href{http://www.ges.cz}{GES Electronics}									&	$ 8 $ & $\textrm{Kč} $	\\
		$ 1 $ & $\mathrm{ks} $ & regulátor napětí 								&	\href{http://www.gme.cz/cz/lm350t-p331-007.html}{LM350T}																						&	\href{http://www.gme.cz}{GM Electronic}										&	$ 38 $ & $\textrm{Kč} $	\\	
		$ 1 $ & $\mathrm{ks} $ & chladič regulátoru 								&	\href{http://www.gme.cz/cz/v4330k-p620-018.html}{V4330K}																						&	\href{http://www.gme.cz}{GM Electronic}										&	$ 48 $ & $\textrm{Kč} $	\\	
		$ 1 $ & $\mathrm{ks} $ & regulátor napětí 								&	\href{http://www.gme.cz/cz/-p330-014.html}{78L09}																										&	\href{http://www.gme.cz}{GM Electronic}										&	$ 6 $ & $\textrm{Kč} $	\\	
		$ 4 $ & $\mathrm{ks} $ & přístrojová svorka červená 				&	\href{http://www.gme.cz/cz/k201r-p808-038.html}{K201R}																								&	\href{http://www.gme.cz}{GM Electronic}										&	$ 16 $ & $\textrm{Kč} $	\\
		$ 4 $ & $\mathrm{ks} $ & přístrojová svorka černá 				&	\href{http://www.gme.cz/cz/k201-p808-003.html}{K201}																									&	\href{http://www.gme.cz}{GM Electronic}										&	$ 16 $ & $\textrm{Kč} $	\\	
		$ 4 $ & $\mathrm{ks} $ & spínač 													&	\href{http://www.gme.cz/cz/p-sm101-2r3-p624-252.html}{P-SM101-2R3}																	&	\href{http://www.gme.cz}{GM Electronic}										&	$ 9 $ & $\textrm{Kč} $	\\	
		$ 1 $ & $\mathrm{ks} $ & spínač 													&	\href{http://www.gme.cz/cz/p-r13112b-ah-p631-287.html}{P-R13112B AH}																&	\href{http://www.gme.cz}{GM Electronic}										&	$ 16 $ & $\textrm{Kč} $	\\	
		$ 1 $ & $\mathrm{ks} $ & potenciometr $ 1 \, \mathrm{k\Omega} $	&	\href{http://www.gme.cz/cz/-p113-125.html}{PC1221NK001}																			&	\href{http://www.gme.cz}{GM Electronic}										&	$ 12 $ & $\textrm{Kč} $	\\	
		$ 1 $ & $\mathrm{ks} $ & knoflík													&	\href{http://www.gme.cz/cz/-p624-196.html}{P-S1717GF}																								&	\href{http://www.gme.cz}{GM Electronic}										&	$ 7 $ & $\textrm{Kč} $	\\	
		$ 1 $ & $\mathrm{ks} $ & rezistor $ 120 \, \mathrm{\Omega} $	&	\href{http://www.gme.cz/cz/-p110-051.html}{RR 120R}																								&	\href{http://www.gme.cz}{GM Electronic}										&	$ 1 $ & $\textrm{Kč} $	\\	
		$ 1 $ & $\mathrm{ks} $ & panelový LCD voltmetr					 &	\href{http://www.gme.cz/cz/hd-3438-p722-197.html}{HD-3438}																						&	\href{http://www.gme.cz}{GM Electronic}										&	$ 102 $ & $\textrm{Kč} $	\\	
		$ 2 $ & $\mathrm{ks} $ & mřížka pro ventilátor						&	\href{http://www.gme.cz/cz/fg-08-p624-026.html}{FG-08}																									&	\href{http://www.gme.cz}{GM Electronic}										&	$ 15 $ & $\textrm{Kč} $	\\	
		$ 1 $ & $\mathrm{ks} $ & LED $ 10 \, \mathrm{mm} $ červená	&	\href{http://www.gme.cz/cz/l-813srd-c-p511-777.html}{L-813SRD-C}																		&	\href{http://www.gme.cz}{GM Electronic}										&	$ 2 $ & $\textrm{Kč} $	\\	
		$ 1 $ & $\mathrm{ks} $ & průchodka pro LED $ 10 \, \mathrm{mm} $	&	\href{http://www.gme.cz/cz/ldc1000-p624-306.html}{LDC1000}																		&	\href{http://www.gme.cz}{GM Electronic}										&	$ 4 $ & $\textrm{Kč} $	\\	
		$ 4 $ & $\mathrm{ks} $ & přístrojová nožička 							&	\href{http://www.gme.cz/cz/gf2-p623-037.html}{GF2}																											&	\href{http://www.gme.cz}{GM Electronic}										&	$ 4 $ & $\textrm{Kč} $	\\	
		$ 1 $ & $\mathrm{ks} $ & svorkovnice			 							&	\href{http://www.gme.cz/cz/ark1800-10-p821-155.html	}{ARK1800/10}																			&	\href{http://www.gme.cz}{GM Electronic}										&	$ 17 $ & $\textrm{Kč} $	\\	
					&					 & šroubky, vruty, matky 								&																																																			& Železářství Lamex																		&	$ 30 $ & $\textrm{Kč} $	\\	
		\hline\hline
		\multicolumn{5}{|l|}{\textbf{Celkem}} & $ 1\,122 $ & $ \textrm{Kč} $ \\
		\hline
	\end{tabular}
\end{table}

\begin{table}[h]
	\centering
	\caption{Seznam ostatních součástek použitých při stavbě komory.}
	\label{tab:SeznamSoucastek:Ostatni}
	\begin{tabular}[t]{|r@{$\,$}l|p{4.6cm}|p{4.2cm}|p{3.1cm}|r@{$\,$}l|}
		\hline
		$ 6 $ & $\mathrm{m} $ & kabel dvojlinka										&	\href{http://www.ges.cz/-cyh-2x075mm22-0-ges06900210.html}{CYH 2x0,75mm2/2-0}											&	\href{http://www.ges.cz}{GES Electronics}								&	$ 10 $ & $\textrm{Kč} $	\\
		$ 8 $ & $\mathrm{ks} $ & krokosvorka černá								 &	\href{http://www.gme.cz/cz/-p812-027.html}{KROKOSVORKA~35 CERNA}																&	\href{http://www.gme.cz}{GM Electronic}										&	$ 3 $ & $\textrm{Kč} $	\\	
		$ 8 $ & $\mathrm{ks} $ & krokosvorka bílá									 &	\href{http://www.gme.cz/cz/-p812-011.html}{KROKOSVORKA~35 BILA}																		&	\href{http://www.gme.cz}{GM Electronic}										&	$ 4 $ & $\textrm{Kč} $	\\	
		$ 8 $ & $\mathrm{ks} $ & banánek černý									 &	\href{http://www.gme.cz/cz/-p811-017.html}{BANANA BLACK}																						&	\href{http://www.gme.cz}{GM Electronic}										&	$ 13 $ & $\textrm{Kč} $	\\	
		$ 8 $ & $\mathrm{ks} $ & banánek červený								 &	\href{http://www.gme.cz/cz/-p811-004.html}{BANANA RED}																							&	\href{http://www.gme.cz}{GM Electronic}										&	$ 13 $ & $\textrm{Kč} $	\\	
		$ 2 $ & $\mathrm{ks} $ & svorkovnice										 &	\href{http://www.gme.cz/cz/svorkovnice-2-5-6mm2-12xrm8-p821-329.html}{SVORKOVNICE 2.5-6mm2 12xRM8}		&	\href{http://www.gme.cz}{GM Electronic}								&	$ 17 $ & $\textrm{Kč} $	\\	
		$ 2 $ & $\mathrm{ks} $ & svorkovnice										 &	\href{http://www.gme.cz/cz/svorkovnice-1-2-5mm2-12xrm5-5-p821-328.html}{SVORKOVNICE 1-2.5mm2 12xRM5.5}	&	\href{http://www.gme.cz}{GM Electronic}							&	$ 10 $ & $\textrm{Kč} $	\\	
		$ 2 $ & $\mathrm{ks} $ & sekundové lepidlo	 							&	Loctite SuperBond																																									&	 Železářství Lamex																			&	$ 36 $ & $\textrm{Kč} $	\\	
		$ 20 $ & $\mathrm{ks} $ & lepící tyčinka									 &	\href{http://www.gme.cz/cz/f-sn7379b-p731-047.html}{F-SN7379B}																				&	\href{http://www.gme.cz}{GM Electronic}										&	$ 2 $ & $\textrm{Kč} $	\\	
				
		\hline\hline
		\multicolumn{5}{|l|}{\textbf{Celkem}} & $ 490 $ & $ \textrm{Kč} $ \\
		\hline
	\end{tabular}
\end{table}

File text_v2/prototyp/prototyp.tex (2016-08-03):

\chapter{Návrh prvního protoypu}
V této kapitole popisuji návrh prvního prototypu. Tento prototyp byl první realizovanou turbínou, a proto na ní lze najít spoustu i zásadních chyb. I přes to byla stavba této turbíny velkou a neocenitelnou zkušeností.

První prototyp byl navržen pomocí zjednodušené teorie. Hlavním zdrojem informací tehdy byly internetové stránky \cite{ve:ve}. 

Jelikož se jednalo o první turbínu, byl záměrně zvolen hodně malý průměr – 1,5~m. Tento průměr se ukázal pro první pokusy jako ideální. Dobře se s touto velikostí pracuje. Při údržbě není s trochou opatrnosti problém manipulovat se složenou turbínou i v interiéru.

\begin{figure}[H]
	\centering
	
	\caption{Pohled na celý CAD model prvního prototypu}
	\label{prot1}
\end{figure}

\begin{figure}[H]
	\centering
	
	\caption{Pohled na list prvního prototypu}
	\label{prot2}
\end{figure}

Byla také zvolena nízká rychloběžnost turbíny kvůli obavám z hluku. Ty se ukázaly po více než ročním provozu jako neopodstatněné. Nízká rychloběžnost však přinesla jeden neočekávaný negativní efekt. Při nižší rychlosti větru se i turbína otáčí relativně pomalu a vrhá mihotavý stín, který může působit rušivě. Při silnějším větru se však stín přestává mihotat a jeví se jako polostín. Z tohoto důvodu byla při novém návrhu turbíny použita rychloběžnost 5.

Byl použit profil SG6043. Profil byl vybrán hlavně díky jeho vzhledu a jemnosti. Nebyl dále nějak zkoumán. Shodou okolností se později ukázalo, že tento profil je pro použití na větrné turbíně velmi vhodný.

Pro výpočet byl list rozdělen na 7 částí. U osy otáčení byly použity 4 části s tloušťkou 3 cm, jelikož blízko osy otáčení je změna délky tětivy a úhlu náběhu velká. Naopak ke konci listu se tyto změny snižují, a proto byly použity části s~tloušťkou 9, 12 a 15~cm. Pro každou tuto část byl vypočten úhel náběhu a délka tětivy. Následně byly tyto průřezy lineárně spojeny. Na základě těchto dat jsem vytvořil CAD model složený z jednotlivých částí (obrázek \ref{prot1}).

Listy byly zakončeny malým obloukem. Pro navázání na náboj byla přidána jedna část o~tloušťce 1~cm, která má stejnou délku tětivy i úhel náběhu jako předchozí. Na ni navazuje třícentimetrová část, která se sbíhá do kruhu o průměru 2 cm.

Na obrázcích CAD modelu (\ref{prot1} a \ref{prot2}) si lze všimnout největší chyby v návrhu, která v~podstatě znemožnila použití této turbíny pro zisk energie. Je prohozená tlaková a podtlaková strana profilu. Při návrhu jsem se příliš inspiroval klasickými leteckými vrtulemi, které fungují přesně naopak – proud vzduchu urychlují, nikoliv jej zpomalují.

Tato chyba výrazně snižuje podávaný výkon a účinnost této turbíny. Avšak díky použitému profilu neznemožnila zcela funkci turbíny. Při pohledu na graf průběhu součinitele vztlaku v~závislosti na úhlu náběhu (graf \ref{graf:zavislost1}) lze zjistit, že při neoptimálním úhlu náběhu $-5\,^{\circ}$ profil SG6043 stále dosahuje kladné hodnoty součinitele vztlaku. Konkrétně hodnoty 0,36. Součinitel odporu při tomto úhlu náběhu nepatrně vzrostl. Hodnota součinitele vztlaku je $3,5\times$ nižší. Díky tomu turbína dosahuje minimálního výkonu. 

\chapter{Výroba prvního prototypu}
\section{Výroba listů}
V této kapitole popisuji postup a technologii výroby, kterou byly vytvořeny listy prvního prototypu. Dále shrnuji výhody a nevýhody použitého postupu.

Pro výrobu listu bylo nutné zvážit několik požadavků. Prvně je nutné nějakým způsobem dodržet správný tvar. List by měl být vyroben z materiálu, který se dá snadno opracovat a měl by být zvolen postup, kterým jdou vyrobit 3 listy s co nejmenšími odchylkami v jejich tvaru. Dále by měl být použitý materiál co nejlehčí, aby nebyl náboj příliš zatěžován odstředivou silou. List však musí vydržet odpor větru.

Listy jsou vyrobeny ze zbytků zateplovacího polystyrenu. Uvnitř nich je nosná konstrukce složená z ocelové tyče o průměru 10 mm a délce 240 mm (z toho 160 se nachází uvnitř listu). Na tuto kulatinu byla připájena tenčí, pětimilimetrová, kulatina o délce 360 mm, která tvoří výztuhu u konce listu, kde je profil tak tenký, že se zde desetimilimetrová kulatina nevleze. Povrch listů je potažen dvěma vrstvami netkané textilie prosycené lepidlem.

Jednotlivé části listu byly vyříznuty nažhavený drátem (odporový drát připojený na zdroj stejnosměrného proudu) podle připravených šablon z hliníkového plechu. Tyto šablony byly vytvořeny z výše uvedeného CAD modelu. Jejich tvar byl vytištěn na laserové tiskárně a následně přežehlen na hliníkový plech. Tyto šablony pak byly vyříznuty a dobroušeny na požadovaný tvar.

Výroba každé části listu probíhala následovně. Prvně jsem uřízl nažhaveným drátem desku polystyrenu požadované tloušťky. Do ní jsem následně vyvrtal trubkovým vrtákem díru pro nosník. Do díry jsem nasadil pomocný kolík a pomocí něj přilepil oboustrannou lepicí páskou jednu šablonu. Na druhou stranu byla přilepena adekvátní šablona. Jejich vzájemnou pozici určoval kolík v díře pro nosník a pak dále značky vytvořené v CAD modelu. Tyto značky musí s kolíkem ležet v jedné rovině. Tím bylo zajištěno správné zkroucení dané části.

Samotné vyříznutí podle šablon vyžadovalo trochu nácviku a zkoušení. Prvně bylo nutné najít správný proud, který musí drátem téci, aby polystyren řezal, ale nepálil. Dále bylo nutné se naučit, jak drátem táhnout. Problém zde byl v tom, že šablony mají různou velikost a rozdílný obvod. Na jedné straně je tedy nutné drátem táhnout rychleji. To se mi po určitém nácviku nakonec povedlo a~byl jsem schopen řezat bezchybné tvary. Na závěr byly šablony odlepeny pomocí několika kapek technického benzínu, který rozpustil lepidlo lepicí pásky.

Jednotlivé části potom byly slepeny pomocí lepidla UHU por. Části se k sobě lepily nasazené na nosníku, čímž byla zajištěna jejich správná pozice. List byl po slepení přilepen k nosníku. Prvně pomocí lepidla UHU por, to se však ukázalo jako nespolehlivé pro spojení polystyrenu a~kovu. Po několika dnech provozu turbíny jeden z listů vlivem odstředivé síly upadl. Na nosníky proto byla vybroušena plytká drážka ve tvaru spirály a listy byly přilepeny lepidlem Purex. Toto lepidlo při tvrdnutí pění a vyplňuje velký prostor. Proto zateče mezi jednotlivé kuličky polystyrenu a zároveň do drážky na nosníku. Tento spoj se ukázal jako spolehlivý – již přes rok pevně drží.

List byl postupně potažen dvěma vrstvami netkané textilie prosycené lepidlem Herkules. Tato povrchová skořepina dodala listu pevnost a odolnost vůči povětrnostním podmínkám. Původně měl být list ještě natřen epoxidovým lakem pro zvýšení odolnosti. Avšak ani 2 vrstvy netkané textile nejsou dokonale nepropustné a lak se na pokusném listu prosákl dovnitř a rozpustil polystyren. Jak ukázal čas, listy jsou i bez tohoto nátěru dostatečně odolné. List byl na závěr natřen třemi vrstvami bílého latexového nátěru.

Pro statické vyvážení celého rotoru bylo nutné dva listy dovážit olověnými závažíčky o hmotnosti 2 a 1 gram. Tato závažíčka byla přilepena vteřinovým lepidlem. K mému překvapení i po roce provozu stále drží přilepená.

\section{Umístění - gondola, stožár}
Jelikož jediné možné umístění turbíny je na zahrádce, vznikl požadavek na stožár – nesmí mít kotvící lana. Na stožár byl použit 3,5 m dlouhý starý anténní stožár. Pro případnou demontáž není přímo ukotven v zemi.

Do hloubky 1 m byla zabetonována 2 m dlouhá trubka, která slouží jako lože pro stožár. V~případě potřeby je možné tedy stožár z této ukotvené trubky vysunout a schovat. Stožár je v~této trubce jištěn 6 šrouby zašroubovanými do navařených matek. Celé toto kotvení se v~průběhu času ukázalo jako spolehlivé – i při nejvyšší vichřici netrpí základy stožáru nějakými vibracemi.

Gondola, na níž je umístěna turbína, vznikla svařením dvou vinklů k sobě pomocí kolmých kousků pásoviny. Na její spodní stranu bylo přivařeno svislé ložisko, okolo kterého se celá gondola otáčí. Jako ložisko pro samotnou turbínu byl použit starý stejnosměrný elektromotor. Ten byl vložen do gondoly a přitažen kovovými stahovacími páskami. Kormidlo, které řídí natáčení celé gondoly, bylo vyříznuto za plastové desky.

Náboj rotoru byl vytočen z kusu hliníku. Do něj byly vyvrtány díry pro nosníky listů. Na nosníky listů byly vyfrézovány plošky, za které je nosník v náboji přitažen.

Na tento samotný náboj jsem vytvořil ještě kryt. Tento kryt není důležitý z aerodynamického hlediska (u takto malé plochy je jeho přínos minimální), ale má hlavně funkci estetickou a chrání náboj před povětrnostními vlivy. Tento náboj byl vytvořen stejnou technologií jako listy. Vytvořil jsem si 2 šablony z hliníkového plechu. Odporovým drátem jsem si nařezal $30^{\circ}$ výseče. Na tuto výseč jsem nalepil šablony a podle šablony jsem vyřízl část náboje. Následně jsem slepil 12 takto vyříznutých výsečí do plného kruhu. Tím vznikl základní tvar náboje, do kterého jsem ještě vyvrtal otvory pro nosníky listů a otvory pro utažení šroubů. Náboj nebyl potažen netkanou textilií – jeho tvar by se špatně potahoval. Byl pouze natřen latexovým nátěrem. Po roce provozu se nátěr začal mírně loupat a na polystyrenu byla patrná deformovaná místa od UV záření.

\chapter{Zkušenosti s provozem}

První prototyp byl vyroben na přelomu září a října 2010. Stožár i s turbínou byl umístěn 29.~října. Od té doby byla turbíny nepřetržitě v provozu.

První problém nastal dva týdny po instalaci – tehdy, jak jsem zmínil výše, upadlo polystyrenové tělo z nosníku. Po změně lepidla se tento problém již znovu neobjevil.

Zhruba po půlroce se ukázalo vertikální ložisko turbíny jako nespolehlivé. Vlivem změny teplot v něm kondenzovala voda a ložisko zarezlo. Po jeho úpravě funguje spolehlivě.

Další problém se netýkal turbíny samotné, ale jejího uložení. Vlivem povětrnostních podmínek se v září 2011 odlepil jeden permanentní magnet uvnitř motoru použitého jako ložisko a začal drhnout o rotor. Motor vydával skřípavý zvuk. Jelikož však motor nelze použít jako generátor (díky nízkým otáčkám turbíny), stačilo uvolněný magnet vytáhnout.

Celá konstrukce turbíny se během roku provozu osvědčila. Původní obavy z hlučnosti se nepotvrdily. Turbína byla i při sebesilnějším větru tichá. Aby byl vůbec slyšet nějaký hluk, musel člověk stát přímo pod stožárem. Ale i tak nebyl hluk větší než např. šumění listí stromů v okolí.
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

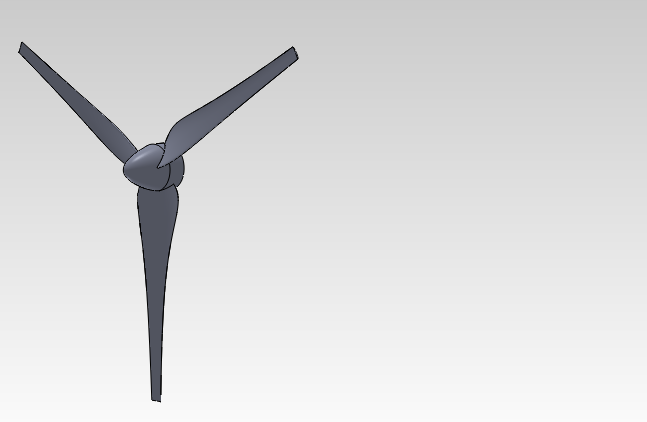
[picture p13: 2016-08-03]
img/Výstřižek2.PNG

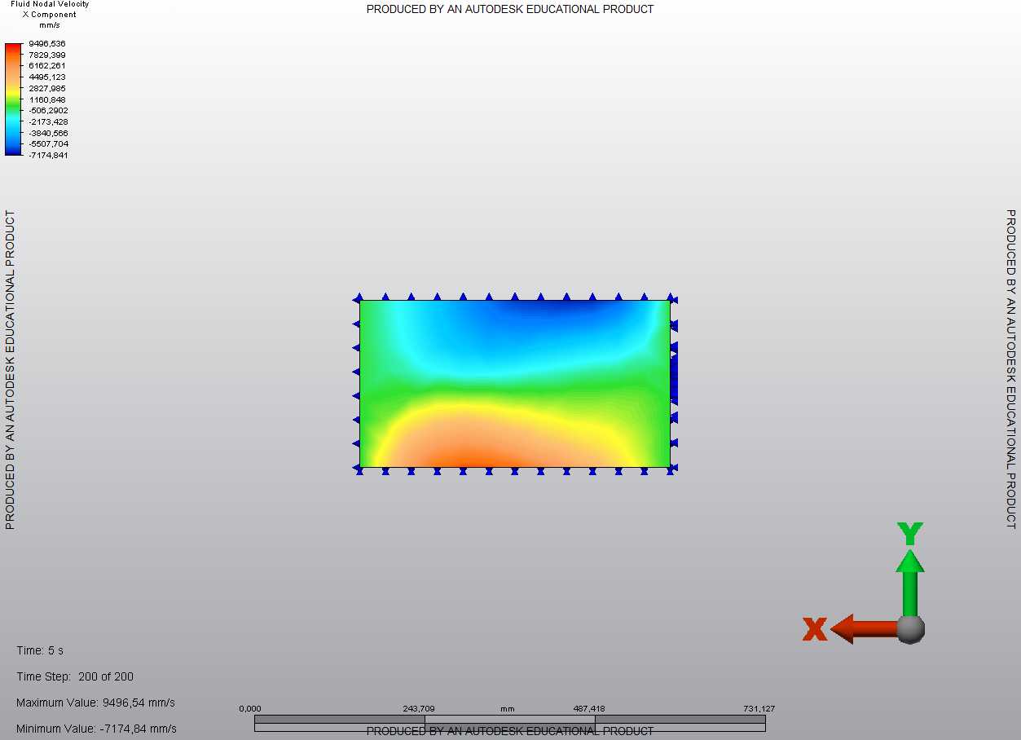
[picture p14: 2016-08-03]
text_v2/simulace/simulace1.jpg

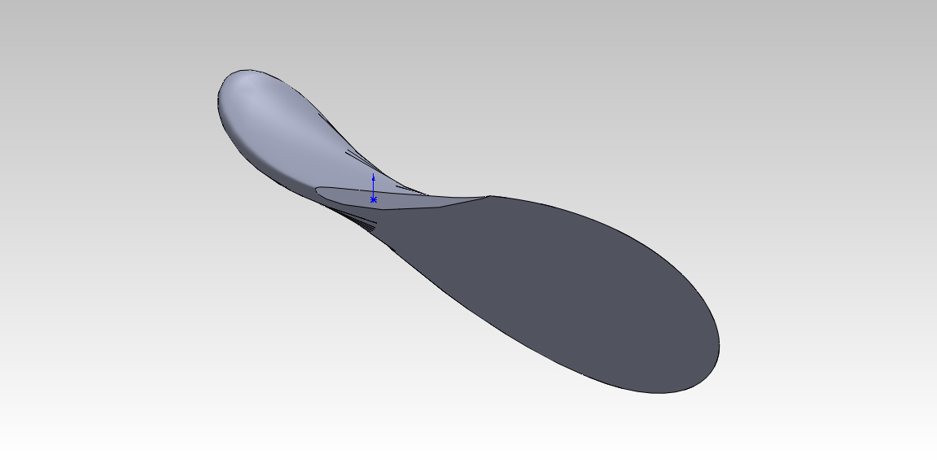
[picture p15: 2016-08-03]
text_v2/Obrazky/rotor/list2.JPG

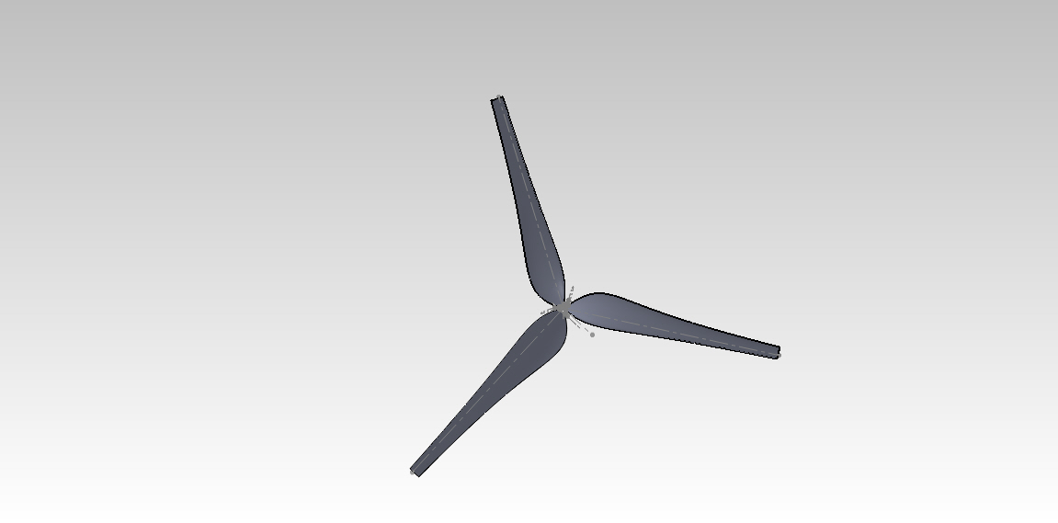
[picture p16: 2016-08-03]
text_v2/Obrazky/rotor/celek.JPG

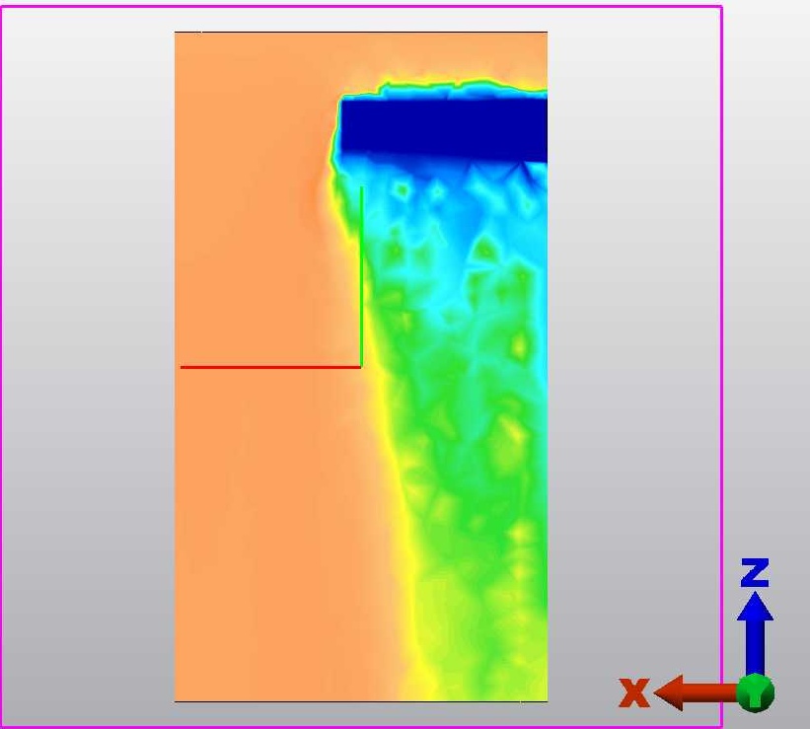
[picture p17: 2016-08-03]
text_v2/Obrazky/simulace/simulace2.jpg

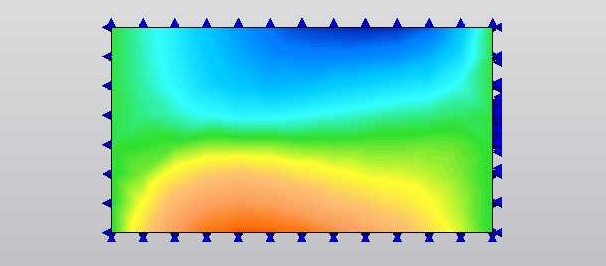
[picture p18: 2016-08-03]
text_v2/Obrazky/simulace/simulace1.jpg

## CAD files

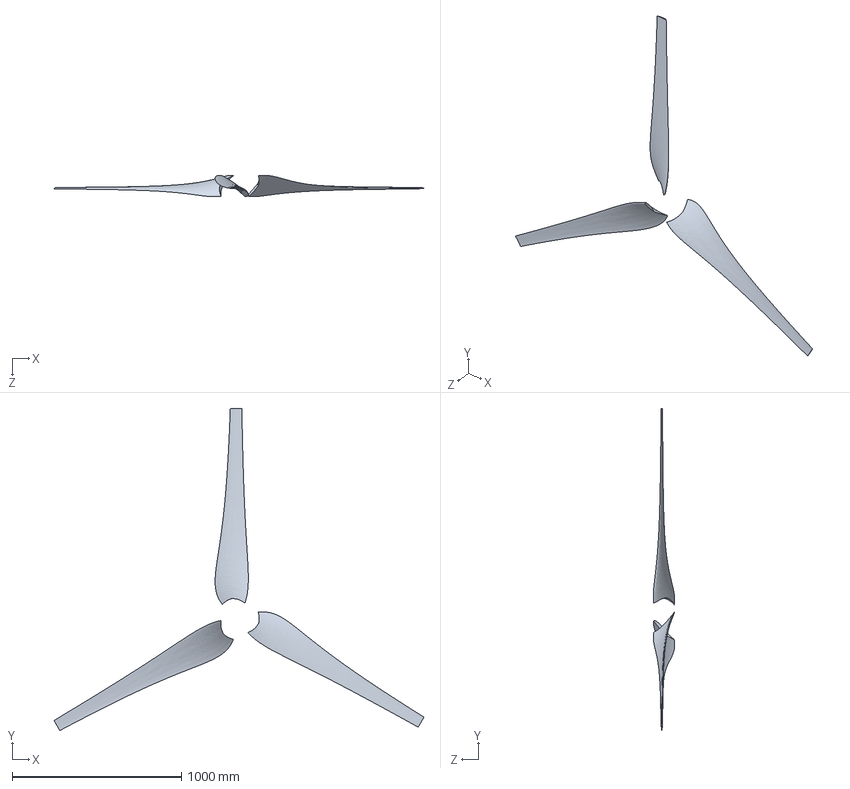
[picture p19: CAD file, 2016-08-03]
new_rotor/Nový rotor/celek.SLDASM
2188.5 x 1905.3 x 126.8 mm
Nový list x 3

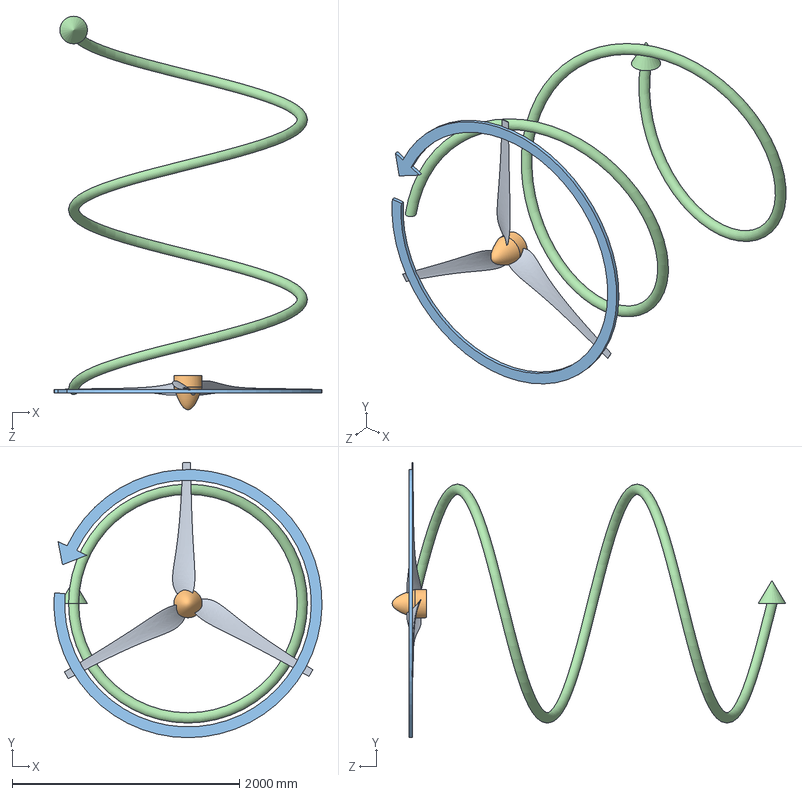
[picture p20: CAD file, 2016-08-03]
new_rotor/Nový rotor/celek. se šipkamiSLDASM.SLDASM
2360.0 x 2424.4 x 3466.0 mm
Nový list x 3
Díl3
Díl1^celek. se šipkamiSLDASM
Díl2^celek. se šipkamiSLDASM

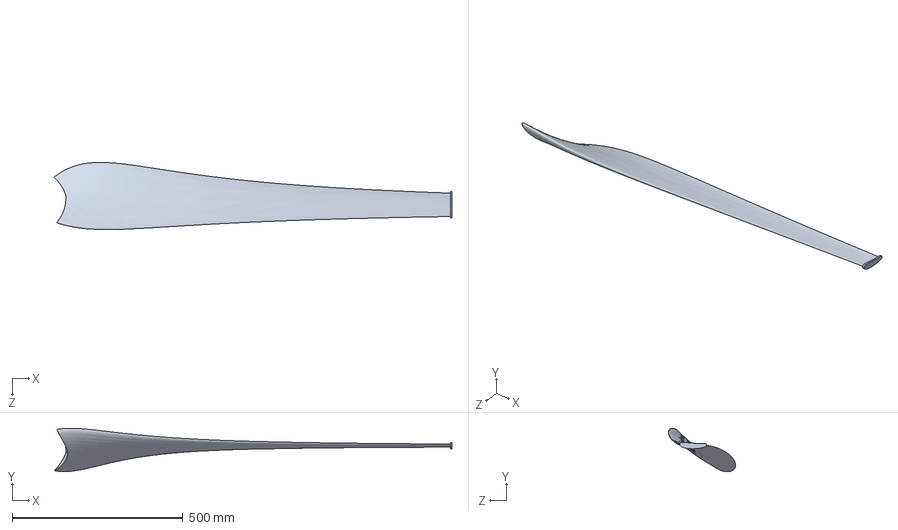
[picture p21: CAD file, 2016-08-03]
new_rotor/Nový rotor/Nový list - zakončení - 5 mm odsazení.SLDPRT
1164.8 x 126.8 x 196.6 mm

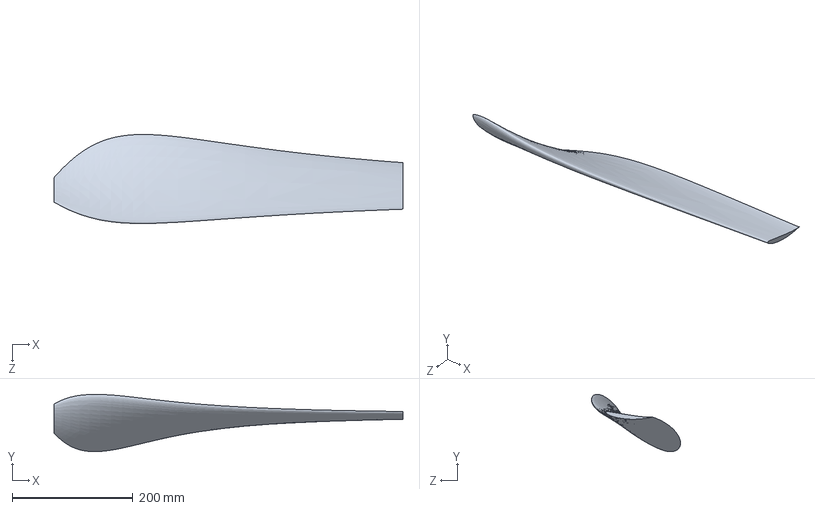
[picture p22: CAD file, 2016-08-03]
new_rotor/První protopy podle Gleuerta/list.SLDPRT
577.5 x 94.8 x 147.4 mm

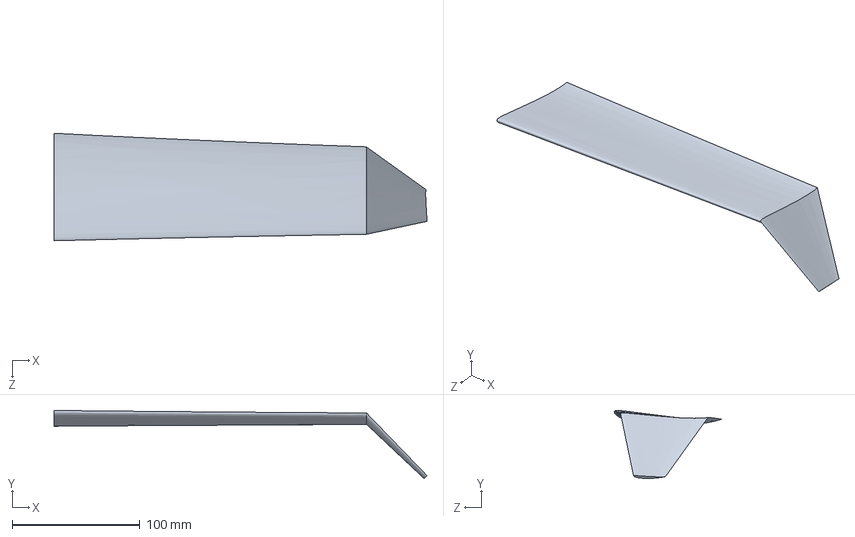
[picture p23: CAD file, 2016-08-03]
new_rotor/Nový rotor/Nový list winglet.SLDPRT
292.4 x 53.4 x 84.3 mm

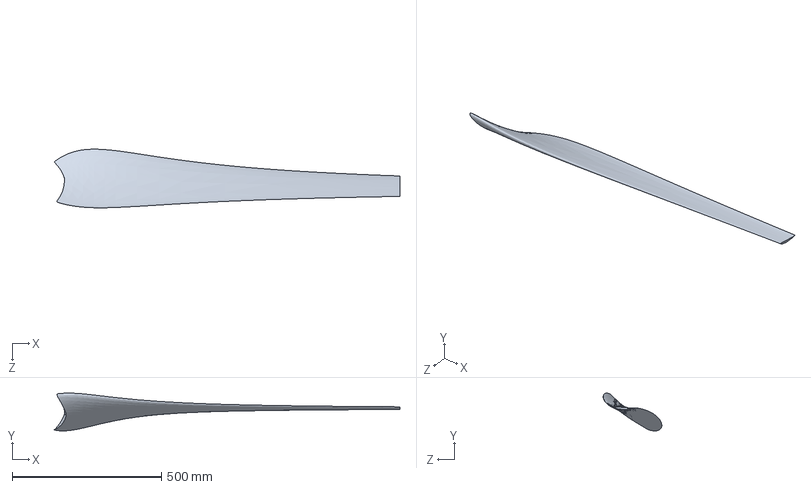
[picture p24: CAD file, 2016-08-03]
new_rotor/Nový rotor/Nový list.SLDPRT
1159.8 x 126.8 x 196.6 mm

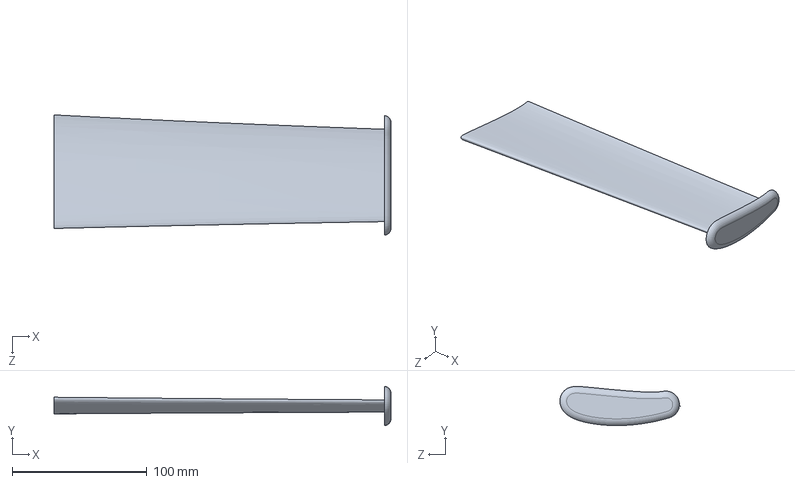
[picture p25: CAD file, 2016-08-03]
new_rotor/Nový rotor/Nový list - zakončení - 10 mm odsazení, zaobleno 1.SLDPRT
250.0 x 29.1 x 89.2 mm

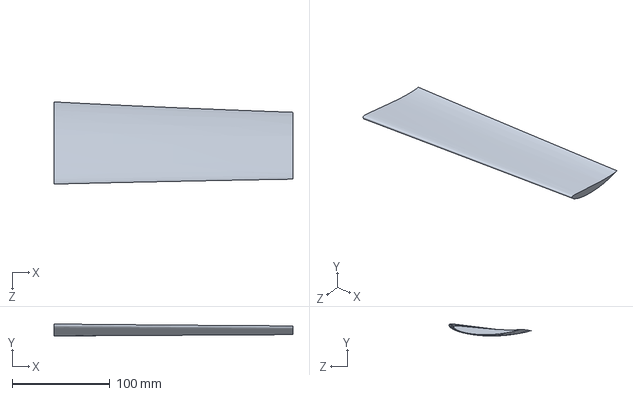
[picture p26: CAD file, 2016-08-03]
new_rotor/Nový rotor/Nový list - zakončení - nic.SLDPRT
245.0 x 12.4 x 84.3 mm

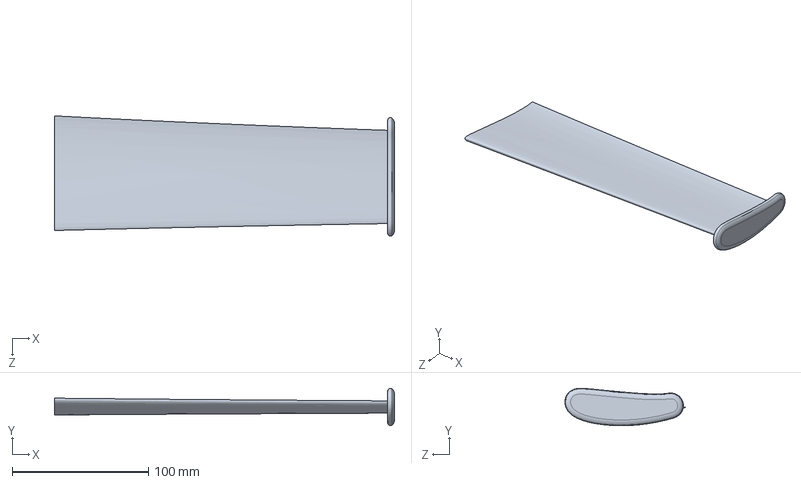
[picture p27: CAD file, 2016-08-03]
new_rotor/Nový rotor/Nový list - zakončení - 10 mm odsazení zaobleno obje.SLDPRT
250.0 x 27.5 x 88.4 mm

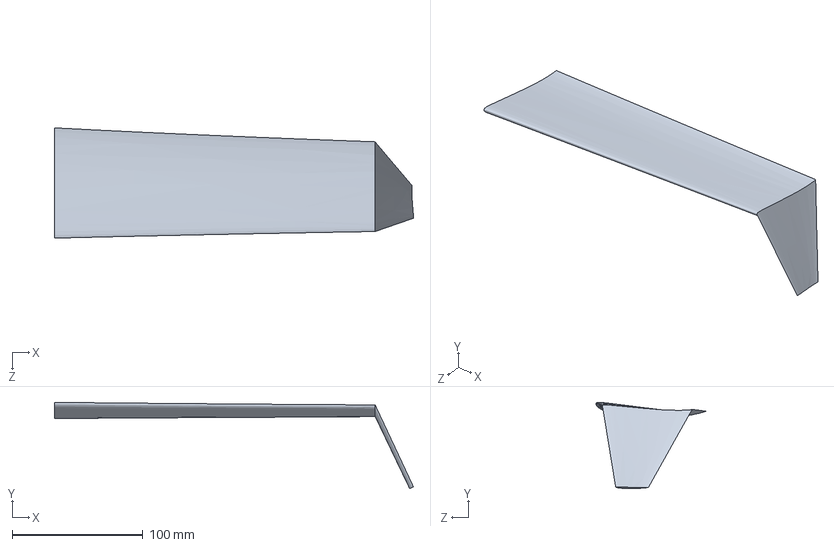
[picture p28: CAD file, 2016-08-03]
new_rotor/Nový rotor/Nový list - zakončení - winglet 65.SLDPRT
274.3 x 66.0 x 84.3 mm

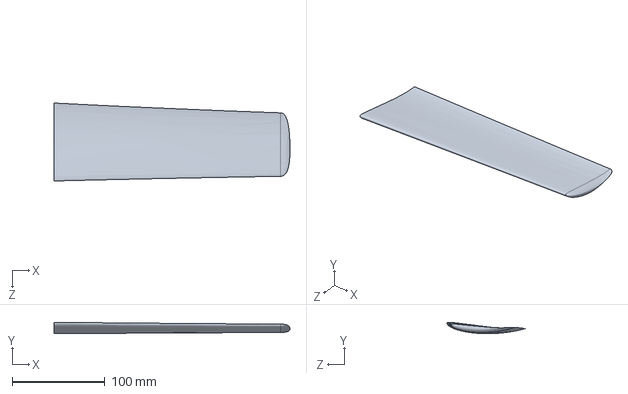
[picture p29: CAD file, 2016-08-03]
new_rotor/Nový rotor/Nový list - zakončení.SLDPRT
255.0 x 12.4 x 84.3 mm

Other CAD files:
profile_simulation/GOE 481A.SLDPRT
new_rotor/Nový rotor/Díl3.sldprt
profile_simulation/WORTMANN FX 60-126-SW.SLDPRT
profile_simulation/SG6043.SLDPRT
profile_simulation/EPPLER 395.SLDPRT
new_rotor/Nový rotor/list.SLDPRT
new_rotor/Nový rotor/Nový list - zakončení kopule.SLDPRT
new_rotor/porovnani.SLDDRW
profile_simulation/EPPLER 395.DWG
profile_simulation/EPPLER 395.SLDDRW
profile_simulation/GOE 481A.DWG
profile_simulation/GOE 481A.SLDDRW
profile_simulation/SG6043.DWG
profile_simulation/SG6043.SLDDRW
profile_simulation/WORTMANN FX 60-126-SW.DWG
profile_simulation/WORTMANN FX 60-126-SW.SLDDRW
